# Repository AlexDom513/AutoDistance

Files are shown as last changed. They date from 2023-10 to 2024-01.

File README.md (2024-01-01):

# autoDistance
The goal of this project is to implement a simple [PID controller](https://en.wikipedia.org/wiki/Proportional%E2%80%93integral%E2%80%93derivative_controller) using a FPGA. [(1)](https://www.youtube.com/watch?v=JFTJ2SS4xyA) and [(2)](https://www.youtube.com/watch?v=oy58S4beC9c) served as the inspiration for this project. Note that a FPGA is being used as an exercise. It is much more convenient to use a microcontroller for this application.

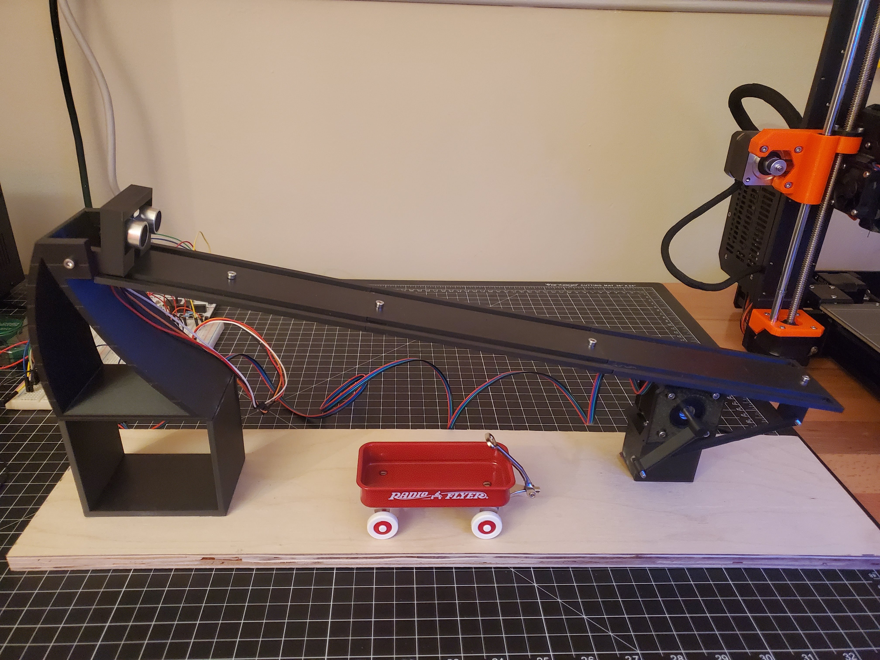
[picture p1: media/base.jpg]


## PID Algorithm
Before starting to implement the PID controller in hardware, a [Python script](https://github.com/AlexDom513/autoDistance/blob/main/algo-dev/algo2.py) was used to understand the algorithm and the system it would be used in. The script was set up in such a way that the user can specify variables like the set-point, the PID gains, and the cart mass.

A simulation then shows how the cart position is affected by the changing angle of a ramp:

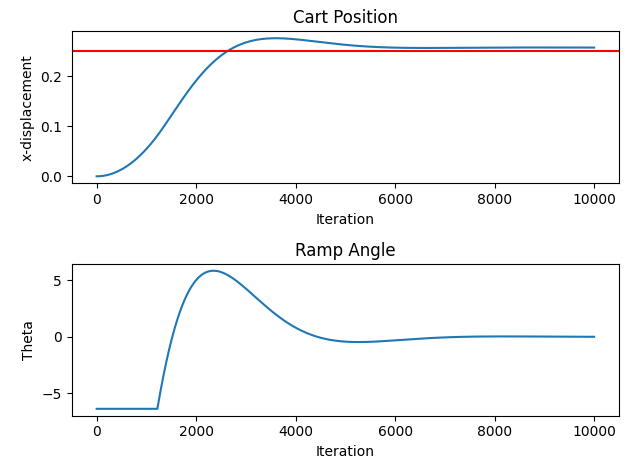
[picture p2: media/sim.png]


## FPGA Modules
### PulseController
The [PulseController](https://github.com/AlexDom513/autoDistance/blob/main/fpga-source/source/PulseController.vhd) module is responsible for interacting with the ultrasonic sensor. According to the [datasheet](https://github.com/AlexDom513/autoDistance/blob/main/datasheets/HCSR04.pdf), the FPGA must send a 10 microsecond trigger pulse. The sensor the sends eight 40 kHz pulses and detects whether there is a returned pulse. If there is a returned pulse, the time of high output from the sensor is proportional to the distance detected.

### PIDController
After obtaining the cart distance in the PulseController module, the [PIDController](https://github.com/AlexDom513/autoDistance/blob/main/fpga-source/source/PidController.vhd) module is used to compute an appropriate ramp angle so that the cart will be directed towards the ramp's center. Proportional gain (P) is a function of where the cart is located along the ramp. Integral gain (I) continues to increase while the cart's observed position is different from the target position. Derivative gain (D) is dependent on how quickly the cart is approaching the target position. A state machine is used to jump between states that contain different computations (error, gains, ramp angle, scaling/saturation).

### StepperController
Whenever a new ramp angle is computed, it is passed to the [StepperController](https://github.com/AlexDom513/autoDistance/blob/main/fpga-source/source/StepperController.vhd) module. This module translates the value into physical movement by the stepper motor attached to the ramp. Two state machines are used to implement this functionality (Stepper State Machine & Pulse State Machine). The Stepper State Machine has a counter that is used to track the position of the stepper motor. The counter is set to 0 during startup. We then monitor whether the output from PIDController is greater than or less than the current value of the counter. Depending on the condition, we will either have the stepper motor increment or decrement from its current position. A signal that controls the motor's direction is set low/high and the Pulse State Machine is used to send trigger pulses to a [A4988](https://components101.com/modules/a4988-stepper-motor-driver-module) motor controller. The stepper motor finally increments or decrements in the desired direction.

## Circuit Schematics
Note: toggled controlled signals (via switches) are NOT shown

### Sensor Circuit
Converts the +3.3V Trig_Pulse signal to +5V logic. Signal is connected to ultrasonic sensor (HC-SR04). The sensor outputs a +5V signal which is converted back to +3.3V before being passed to the FPGA.

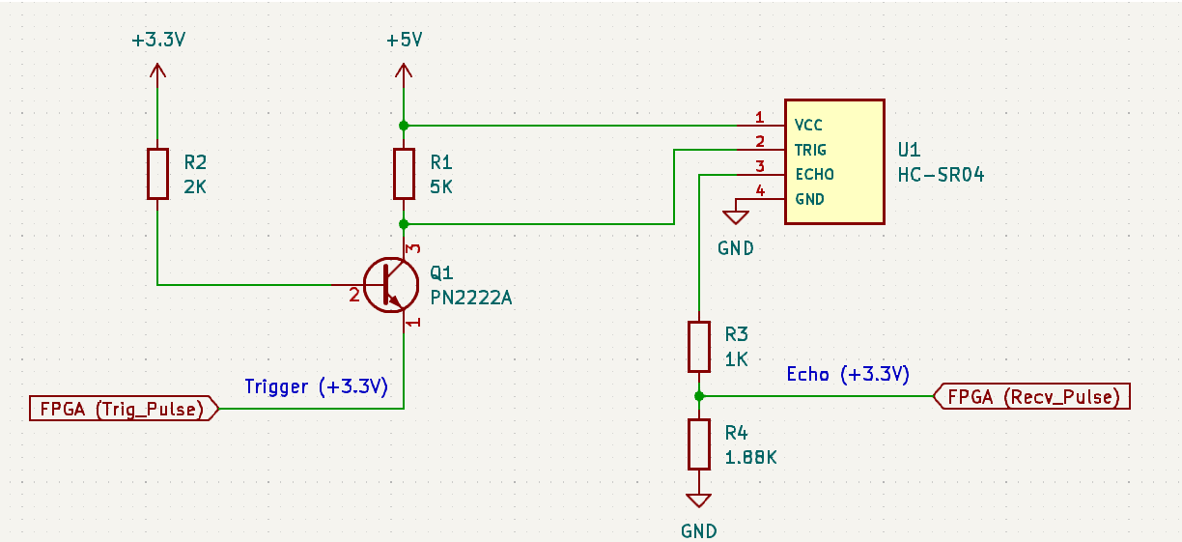
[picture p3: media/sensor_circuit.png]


### Stepper Circuit
Connects control signals (Step_Pulse, Dir_Sel) from the FPGA to the stepper control board (A4988). Since the design is using 1/8 microstepping, MS1 and MS2 are also tied to +5V.

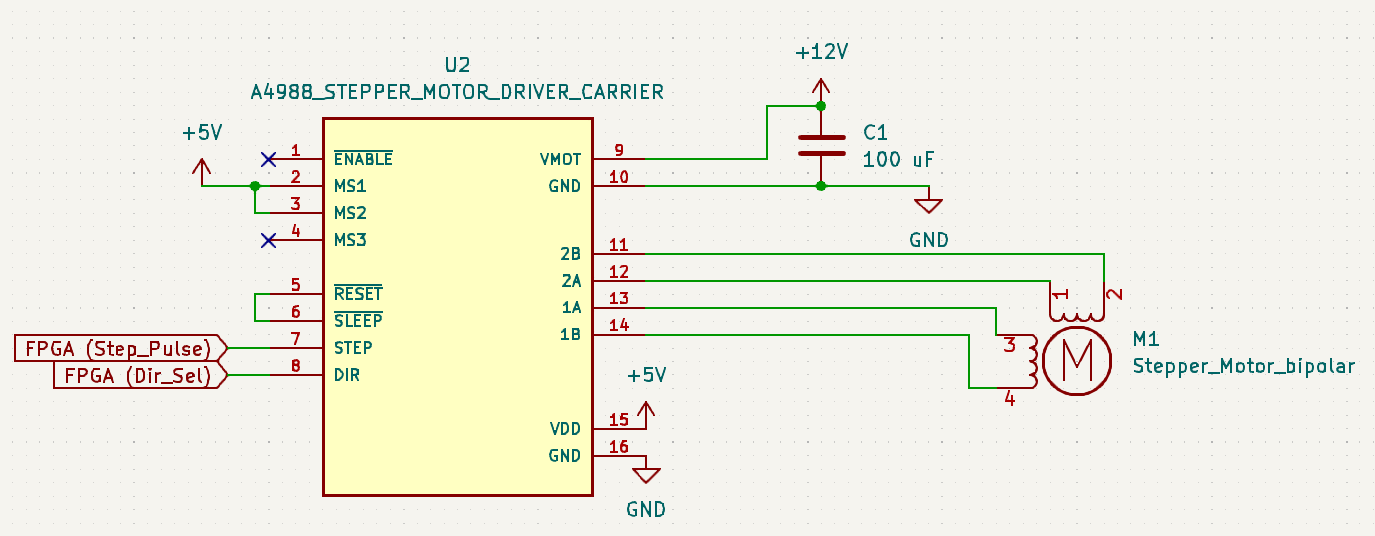
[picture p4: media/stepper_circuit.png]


## CAD
This was my first serious attempt at creating a 3D model! All parts were printed using PLA on a PRUSA MK3.

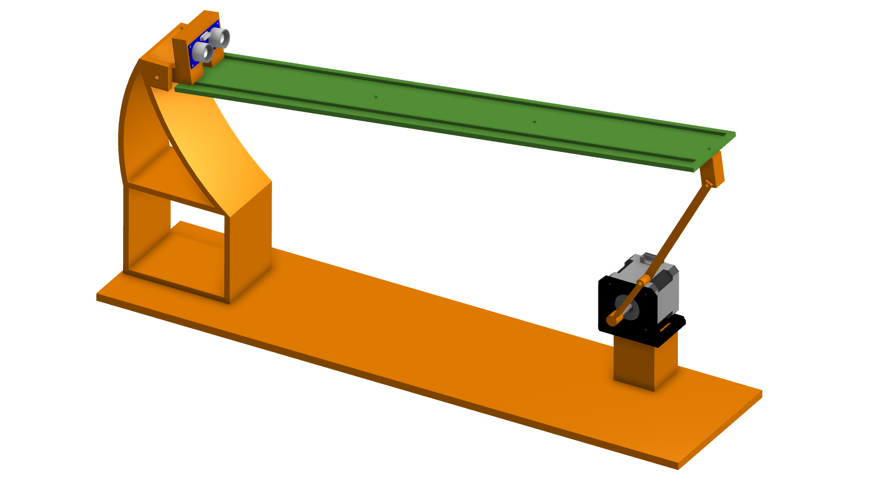
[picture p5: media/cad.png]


[My Parts](https://cad.onshape.com/documents/018887aac5e3fe98b3ecc4ac/w/28ee8de5f592833dfd0388a2/e/8ab51c28ebdef6fccae7c0ab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) |
[HC-SR04 Model](https://grabcad.com/library/hcsr04-ultrasonic-sensor-1) |
[NEMA-17 Model](https://grabcad.com/library/nema17-42-40-1) |
[Motor Bracket](https://grabcad.com/library/nema-17-stepper-motor-mounting-bracket-2)

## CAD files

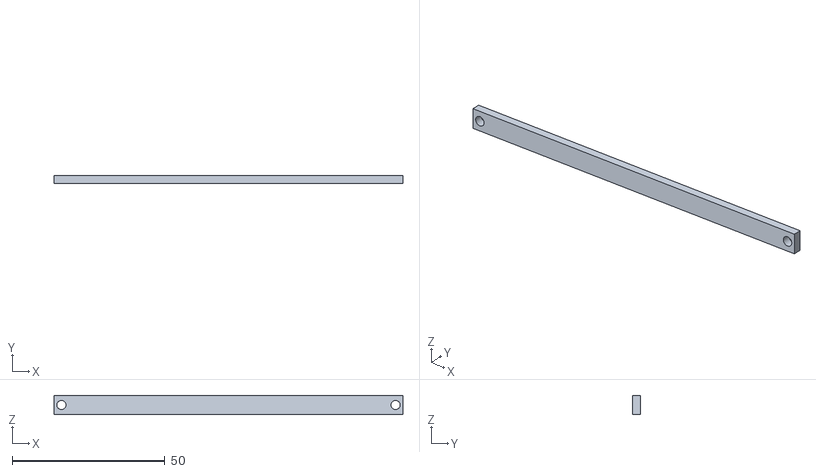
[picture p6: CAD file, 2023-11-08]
CAD-files/Motor Components/Arm.stl
114.3 x 2.54 x 6.35

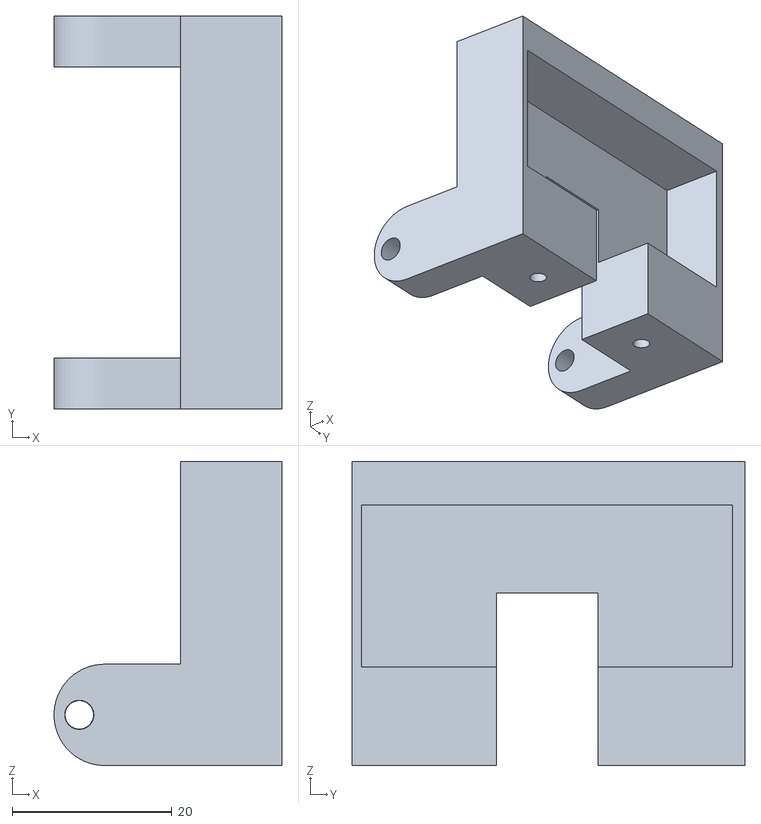
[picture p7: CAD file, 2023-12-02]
CAD-files/Sensor Components/Sensor Mount.stl
28.6 x 49.2 x 38.1

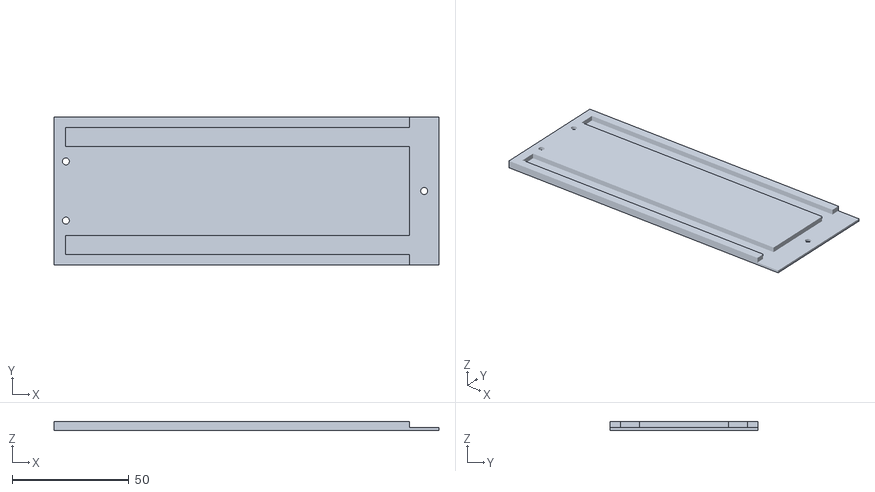
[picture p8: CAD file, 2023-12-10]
CAD-files/Track/Track End w- Sensor Mount.stl
165.1 x 63.5 x 3.81

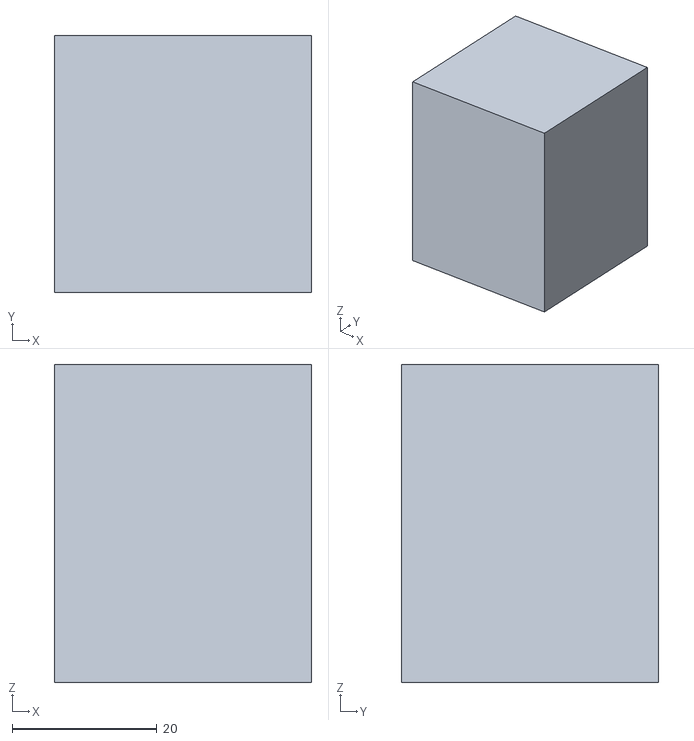
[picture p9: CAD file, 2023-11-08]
CAD-files/Motor Components/Motor Base.stl
35.6 x 35.6 x 43.9

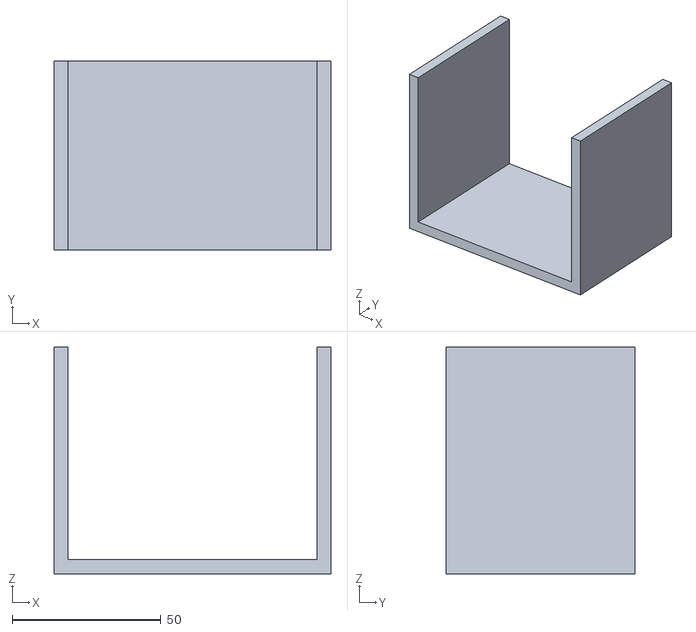
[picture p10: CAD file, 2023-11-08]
CAD-files/Sensor Components/Sensor Base Extension.stl
93.0 x 63.5 x 76.2

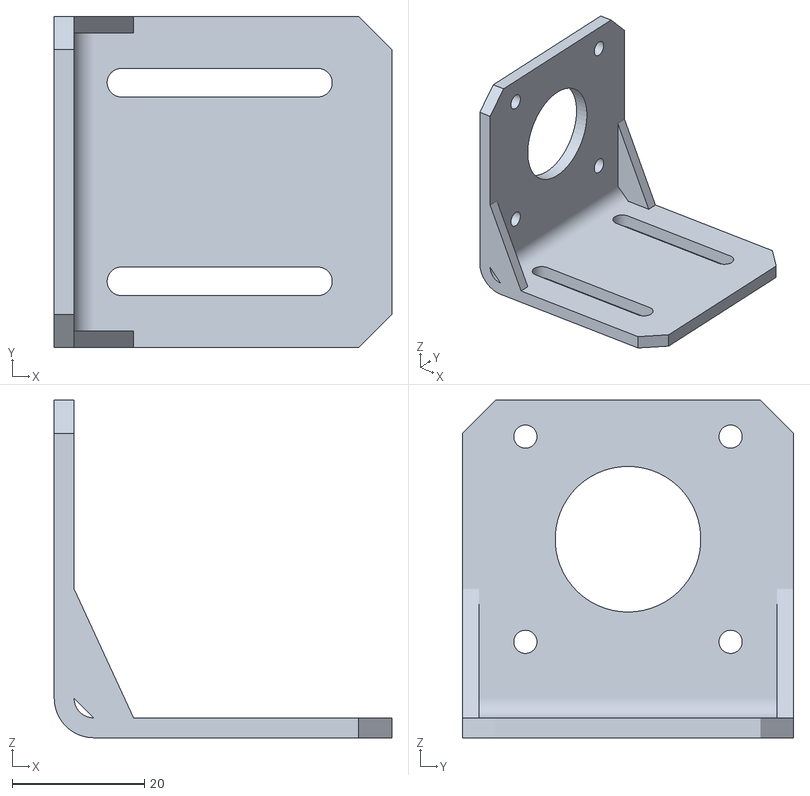
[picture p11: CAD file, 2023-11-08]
CAD-files/Motor Components/Nema_17_Stepper_Motor_Mount.stl
51.0 x 50.0 x 51.0

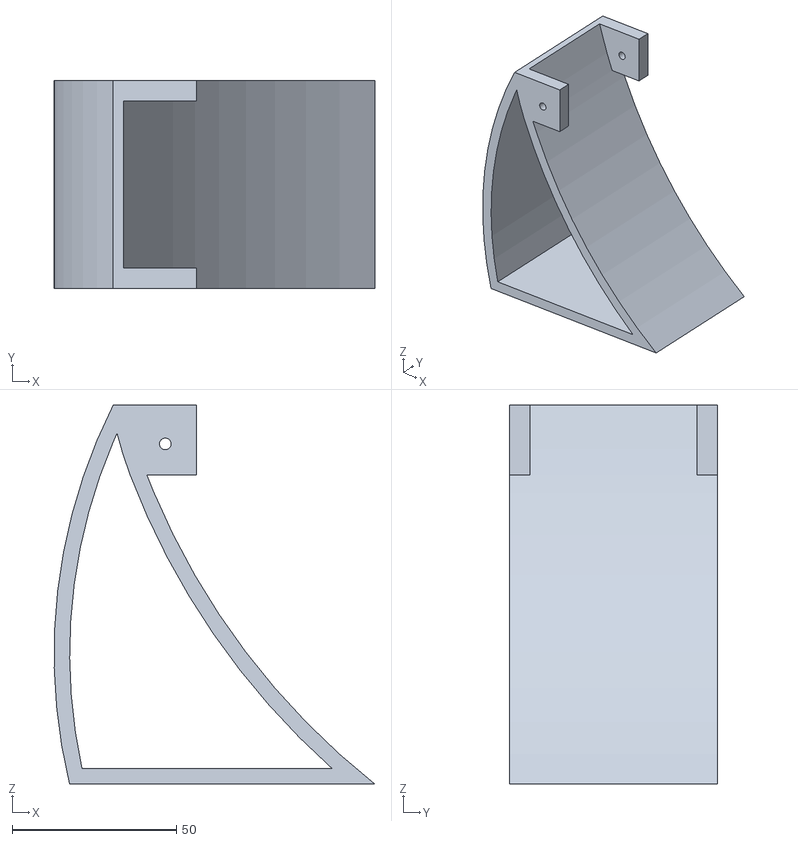
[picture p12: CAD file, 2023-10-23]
CAD-files/Sensor Components/Sensor Base.stl
97.7 x 63.5 x 115.5

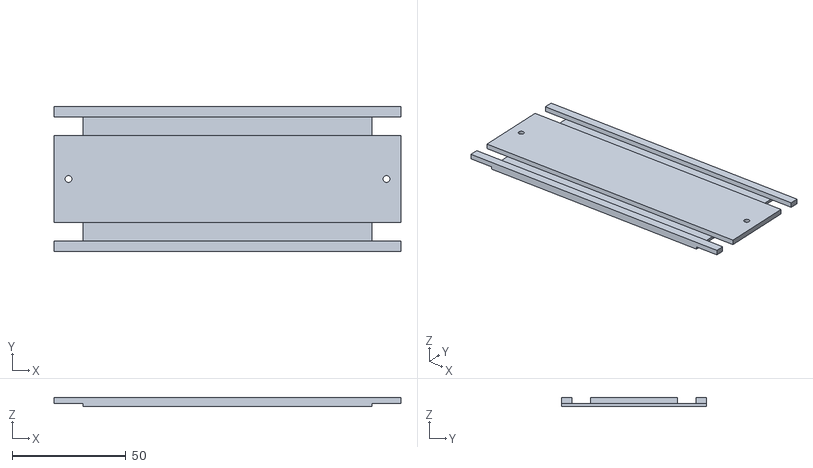
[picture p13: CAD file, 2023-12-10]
CAD-files/Track/Track Center.stl
152.4 x 63.5 x 3.81

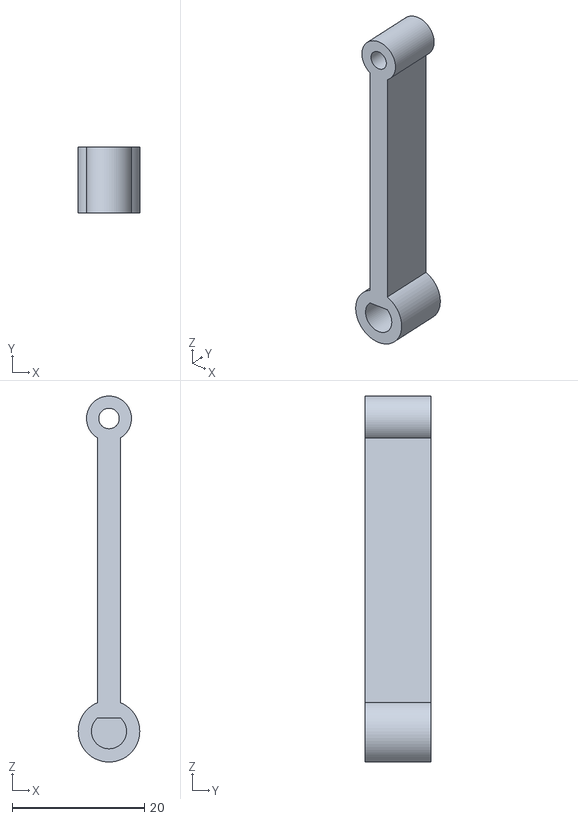
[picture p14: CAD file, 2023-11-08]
CAD-files/Motor Components/Coupler.stl
9.30 x 10.0 x 55.3

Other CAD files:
CAD-files/Track/Track End w- Coupler.stl

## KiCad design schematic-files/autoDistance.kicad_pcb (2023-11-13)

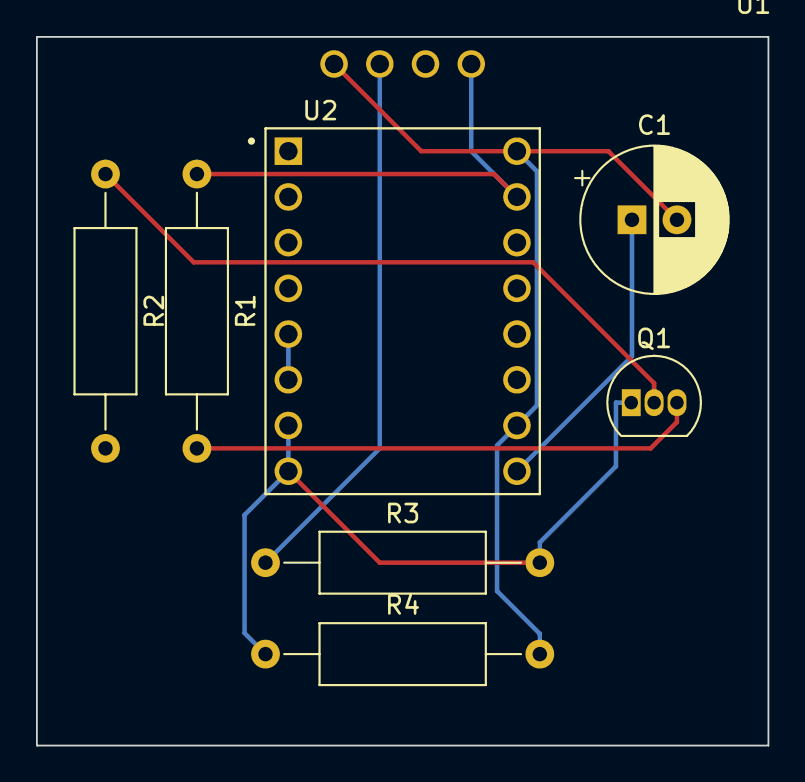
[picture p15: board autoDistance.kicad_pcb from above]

Board: 2 copper layers, 40.6 x 39.4 mm, 8 parts (0 on the bottom side), 8 nets.

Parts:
C1: 100 uF; CP_Radial_D8.0mm_P2.50mm
Q1: PN2222A; TO-92_Inline
R1: 5K; R_Axial_DIN0309_L9.0mm_D3.2mm_P15.24mm_Horizontal
R2: 2K; R_Axial_DIN0309_L9.0mm_D3.2mm_P15.24mm_Horizontal
R3: 1K; R_Axial_DIN0309_L9.0mm_D3.2mm_P15.24mm_Horizontal
R4: 1.88K; R_Axial_DIN0309_L9.0mm_D3.2mm_P15.24mm_Horizontal
U1: HC-SR04; XCVR_HC-SR04
U2: A4988_STEPPER_MOTOR_DRIVER_CARRIER; MODULE_A4988_STEPPER_MOTOR_DRIVER_CARRIER

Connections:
+5V: R1.1, U1.1 (VCC), U2.15 (VDD)
+12V: C1.1, U2.9 (VMOT)
ARTY: Q1.1 (E), R3.2, R4.1, U2.7 (STEP), U2.8 (DIR)
GND: C1.2, R4.2, U1.4 (GND), U2.10 (GND), U2.16 (GND)
unnamed: Q1.2 (B), R2.1
unnamed: Q1.3 (C), R1.2, U1.2 (TRIG)
unnamed: R3.1, U1.3 (ECHO)
unnamed: U2.5 (~RESET), U2.6 (~SLEEP)

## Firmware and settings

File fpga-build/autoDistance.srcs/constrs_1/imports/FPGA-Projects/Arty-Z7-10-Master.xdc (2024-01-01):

## This file is a general .xdc for the ARTY Z7-10 Rev.B
## To use it in a project:
## - uncomment the lines corresponding to used pins
## - rename the used ports (in each line, after get_ports) according to the top level signal names in the project

## Clock Signal
set_property -dict {PACKAGE_PIN H16 IOSTANDARD LVCMOS33} [get_ports Clk]
#create_clock -period 2.000 -name sys_clk_pin -waveform {0.000 1.000} -add [get_ports Clk]
create_clock -period 8.000 -name sys_clk_pin -waveform {0.000 4.000} -add [get_ports Clk]

## Switches
set_property -dict {PACKAGE_PIN M20 IOSTANDARD LVCMOS33} [get_ports Rst]
set_property -dict {PACKAGE_PIN M19 IOSTANDARD LVCMOS33} [get_ports Init_Pos_Sel]

## RGB LEDs
#set_property -dict { PACKAGE_PIN L15    IOSTANDARD LVCMOS33 } [get_ports { led4_b }]; #IO_L22N_T3_AD7P_35 Sch=LED4_B
#set_property -dict { PACKAGE_PIN G17    IOSTANDARD LVCMOS33 } [get_ports { led4_g }]; #IO_L16P_T2_35 Sch=LED4_G
#set_property -dict { PACKAGE_PIN N15    IOSTANDARD LVCMOS33 } [get_ports { led4_r }]; #IO_L21P_T3_DQS_AD14P_35 Sch=LED4_R
#set_property -dict { PACKAGE_PIN G14    IOSTANDARD LVCMOS33 } [get_ports { led5_b }]; #IO_0_35 Sch=LED5_B
#set_property -dict { PACKAGE_PIN L14    IOSTANDARD LVCMOS33 } [get_ports { led5_g }]; #IO_L22P_T3_AD7P_35 Sch=LED5_G
#set_property -dict { PACKAGE_PIN M15    IOSTANDARD LVCMOS33 } [get_ports { led5_r }]; #IO_L23N_T3_35 Sch=LED5_R

## LEDs
set_property -dict {PACKAGE_PIN R14 IOSTANDARD LVCMOS33} [get_ports Led0]
set_property -dict {PACKAGE_PIN P14 IOSTANDARD LVCMOS33} [get_ports Led1]
set_property -dict {PACKAGE_PIN N16 IOSTANDARD LVCMOS33} [get_ports Led2]
set_property -dict {PACKAGE_PIN M14 IOSTANDARD LVCMOS33} [get_ports Led3]

## Buttons
#set_property -dict { PACKAGE_PIN D19    IOSTANDARD LVCMOS33 } [get_ports { btn[0] }]; #IO_L4P_T0_35 Sch=BTN0
#set_property -dict { PACKAGE_PIN D20    IOSTANDARD LVCMOS33 } [get_ports { btn[1] }]; #IO_L4N_T0_35 Sch=BTN1
#set_property -dict { PACKAGE_PIN L20    IOSTANDARD LVCMOS33 } [get_ports { btn[2] }]; #IO_L9N_T1_DQS_AD3N_35 Sch=BTN2
#set_property -dict { PACKAGE_PIN L19    IOSTANDARD LVCMOS33 } [get_ports { btn[3] }]; #IO_L9P_T1_DQS_AD3P_35 Sch=BTN3

## Pmod Header JA
#set_property -dict { PACKAGE_PIN Y18   IOSTANDARD LVCMOS33 } [get_ports { ja_p[1] }]; #IO_L17P_T2_34 Sch=JA1_P (Pin 1)
#set_property -dict { PACKAGE_PIN Y19   IOSTANDARD LVCMOS33 } [get_ports { ja_n[1] }]; #IO_L17N_T2_34 Sch=JA1_N (Pin 2)
#set_property -dict { PACKAGE_PIN Y16   IOSTANDARD LVCMOS33 } [get_ports { ja_p[2] }]; #IO_L7P_T1_34 Sch=JA2_P (Pin 3)
#set_property -dict { PACKAGE_PIN Y17   IOSTANDARD LVCMOS33 } [get_ports { ja_n[2] }]; #IO_L7N_T1_34 Sch=JA2_N (Pin 4)
#set_property -dict { PACKAGE_PIN U18   IOSTANDARD LVCMOS33 } [get_ports { ja_p[3] }]; #IO_L12P_T1_MRCC_34 Sch=JA3_P (Pin 7)
#set_property -dict { PACKAGE_PIN U19   IOSTANDARD LVCMOS33 } [get_ports { ja_n[3] }]; #IO_L12N_T1_MRCC_34 Sch=JA3_N (Pin 8)
#set_property -dict { PACKAGE_PIN W18   IOSTANDARD LVCMOS33 } [get_ports { ja_p[4] }]; #IO_L22P_T3_34 Sch=JA4_P (Pin 9)
#set_property -dict { PACKAGE_PIN W19   IOSTANDARD LVCMOS33 } [get_ports { ja_n[4] }]; #IO_L22N_T3_34 Sch=JA4_N (Pin 10)

## Pmod Header JB
#set_property -dict { PACKAGE_PIN W14   IOSTANDARD LVCMOS33 } [get_ports { jb_p[1] }]; #IO_L8P_T1_34 Sch=JB1_P (Pin 1)
#set_property -dict { PACKAGE_PIN Y14   IOSTANDARD LVCMOS33 } [get_ports { jb_n[1] }]; #IO_L8N_T1_34 Sch=JB1_N (Pin 2)
#set_property -dict { PACKAGE_PIN T11   IOSTANDARD LVCMOS33 } [get_ports { jb_p[2] }]; #IO_L1P_T0_34 Sch=JB2_P (Pin 3)
#set_property -dict { PACKAGE_PIN T10   IOSTANDARD LVCMOS33 } [get_ports { jb_n[2] }]; #IO_L1N_T0_34 Sch=JB2_N (Pin 4)
#set_property -dict { PACKAGE_PIN V16   IOSTANDARD LVCMOS33 } [get_ports { jb_p[3] }]; #IO_L18P_T2_34 Sch=JB3_P (Pin 7)
#set_property -dict { PACKAGE_PIN W16   IOSTANDARD LVCMOS33 } [get_ports { jb_n[3] }]; #IO_L18N_T2_34 Sch=JB3_N (Pin 8)
#set_property -dict { PACKAGE_PIN V12   IOSTANDARD LVCMOS33 } [get_ports { jb_p[4] }]; #IO_L4P_T0_34 Sch=JB4_P (Pin 9)
#set_property -dict { PACKAGE_PIN W13   IOSTANDARD LVCMOS33 } [get_ports { jb_n[4] }]; #IO_L4N_T0_34 Sch=JB4_N (Pin 10)

## Audio Out
#set_property -dict { PACKAGE_PIN R18   IOSTANDARD LVCMOS33 } [get_ports { aud_pwm }]; #IO_L20N_T3_34 Sch=AUD_PWM
#set_property -dict { PACKAGE_PIN T17   IOSTANDARD LVCMOS33 } [get_ports { aud_sd }]; #IO_L20P_T3_34 Sch=AUD_SD

## Crypto SDA
#set_property -dict { PACKAGE_PIN J15   IOSTANDARD LVCMOS33 } [get_ports { crypto_sda }]; #IO_25_35 Sch=CRYPTO_SDA
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

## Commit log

2023-09-25 file-reorg + algo prototype start
2023-09-29 sim improvements + pid tuning
2023-09-29 added schematic capture
    [ballControl.kicad_pcb, ballControl.kicad_sch]
2023-10-23 mechDev + sim work
    [Holder.3mf, Holder.stl, Sensor Holder.3mf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]
2023-11-01 sim improvements using GHDL and GTKwave
    [Nema17.stl, Track Hybrid Connector.stl, autoDistance.kicad_pcb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]
2023-11-04 ultrasonic functional
2023-11-05 add stepper coupler
    [Coupler.stl, Nema17.stl]
2023-11-08 revamp mechanical design
    [Base Extension.stl, Coupler Connector.stl, Coupler Mount.stl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]
2023-11-13 StepperController Start
    [autoDistance.kicad_pcb, autoDistance.kicad_sch]
2023-11-14 Stepper Controller compiles
2023-11-19 StepperController tested on hardware
2023-11-25 pid module progress
2023-11-26 progress towards proportional gain implementation
    [Sensor Mount.stl]
2023-12-02 proportional control, partially working
    [Sensor Mount.stl]
2023-12-10 project cleanup
    [Arm.stl, Coupler Mount.stl, Coupler.stl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]
2023-12-18 SMA filter
2023-12-27 schematic updates
    [autoDistance.kicad_sch]
2024-01-01 tuning + deadzone + fixes
    [Arty-Z7-10-Master.xdc]
